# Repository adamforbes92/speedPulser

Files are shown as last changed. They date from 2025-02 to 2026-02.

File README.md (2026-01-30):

# SpeedPulser
The SpeedPulser is designed to take digital pulses from a speed sensor within the gearbox and translate this into a PWM signal which drives an OEM speedometer.  It’s perfect for situations where a physical speedometer cable cannot be installed or those wishing for a cleaner installation.  It is budget-friendly and therefore requires some final user setup and calibration.

The SpeedPulser also accepts speed signals from Can2Cluster – which can get speed from the ECU, DSG or GPS inputs.

The device takes the signals and converts them into signals to suit analog clusters – like the MK1 & MK2 Golf.  It is fully opensource and the source code can be downloaded and adjusted to suit other brands if required.  Please get in touch if you need help!

It is based on a Lolin C3 ESP32 and the BLDC motor is a TY3816B.

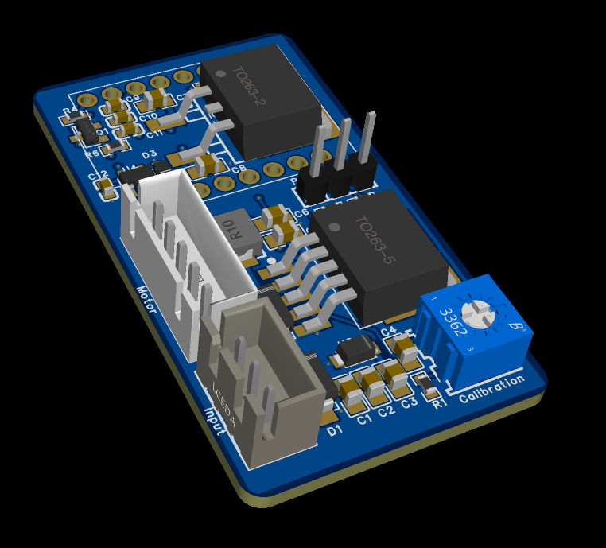
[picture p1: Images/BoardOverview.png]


### Supported Models

> MK1/MK2 Golf (120/140/160mph)
> FIAT (160mph)
> Mercedes W123/W124
> Smiths 5/8" 

Users are actively encouraged to submit new models & calibrations.

### More Detailed Instructions
The last file on GitHub is the 'Installation Guide' and provides more detail.

### Purchase
If you want to purchase an assembled SpeedPulser, you can do so here: [SpeedPulser - Forbes Automotive](https://forbes-automotive.com/products/speedpulser)

#### Installation
Only three wires are required to operate the SpeedPulser:

| Pin/ | Signal | Notes |
|-----|---|---|
| 1 | Vbatt | 12 V |
| 2 | Ground/MALT | — |
| 3 | 12v pulse | Square wave type signal |

For reference, the motor pinout is:
| Pin/ | Signal | Notes |
|-----|---|---|
| 1 | Mpwr | Black - 5-9v adjustable |
| 2 | N/A | Not used |
| 3 | Motor Direction | Green - ground to reverse |
| 4 | Motor Ground | White - motor ground |
| 5 | Motor PWM | 10kHz signal from ESP32 |

#### Pull-up or Pull-down
Different hall sensors from different manufacturers may require a pull-up or pull-down resistor.  There is a 2-way header on the board to select this.  If you find the SpeedPulser is not detecting incoming pulses, move this jumper.  Some hall sensors may have their own internal resistor, so the jumper can be removed entirely.

#### Coupler Installation
The motors will come with the coupler pre-installed and the final drive pin and securing pins separate. The end user should remove the motor and align the drive pin into the coupler and push it home. It will be a  tight fit, but a few light taps will drive it home. A spare coupler is also supplied in the kit. There should be an appreciation that the couplers are 3D printed and therefore may have some alignment variations, this is the chance to lightly heat (~100c max) to encourage/make run true. If the coupling has excessive vibration is may strip out, but a drop of superglue will repair this and run indefinitely. If this is required, ensure that the coupler runs true! Future revisions may look to replace these with a metal alternative, but this would reflect in a higher price. The point of this kit is to remain budget friendly. 

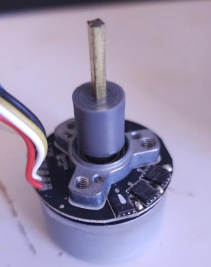
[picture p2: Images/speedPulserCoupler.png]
SpeedPulserCoupler


#### Trimming the Drive Shaft
Drive shafts are supplied in excess of required length and should be trimmed to suit each individual cluster.  Typically this is ~level with the motor housing but confirmation that it is not bottomed out is key!

#### Fine Tuning Coupler
Once the motor is built up, it can be slid over the OEM cluster. Fitment of the drive pin should be confirmed and that the motor spins freely. Some fine tuning here will keep noise to a minimum and reduce the risk of premature failure of the coupler. The drive-pin length should also be confirmed and ensure that it does engage with the cluster but does not bottom out and stop the housing seating fully. Take your time here!

#### Software Benefits
The SpeedPulser is now WiFi capable which means that all of the necessary calibration settings are available for changing in WiFi.  It will store these settings in EEPROM.  
> Fully calibrated motor: Duty Percentage vs. Resulting Speed
> Needle Sweep available
> WiFi Enabled

#### WiFi Support
WiFi is now enabled for easier on-the-fly setup.  Needle sweep & calibration can be done without needing to mess with complicated firmware.
Connect to 'SpeedPulser' on WiFi and use IP Address 192.168.1.1 in your browser to adjust settings!  WiFi is available for the first 30s after powering on the unit and will remain active when there is a connection.  This is to manage the heat generated.  Version 2 PCBs have a larger voltage step-down unit which can manage more heat.

### Initial Calibration
Initial calibration will be carried out using the WiFi feature.

> Connect to SpeedPulser on WiFi
> Go to 192.168.1.1
> Select 'Advanced Controls'
> Select the calibration you wish to use
> Choose 'Test Speed'
> Select 'Go to Speed' and choose the highest value on your cluster
> Adjust the blue potentiometer to the maximum valve
> Use 'Go to Speed' to confirm random speeds and ensure that it matches

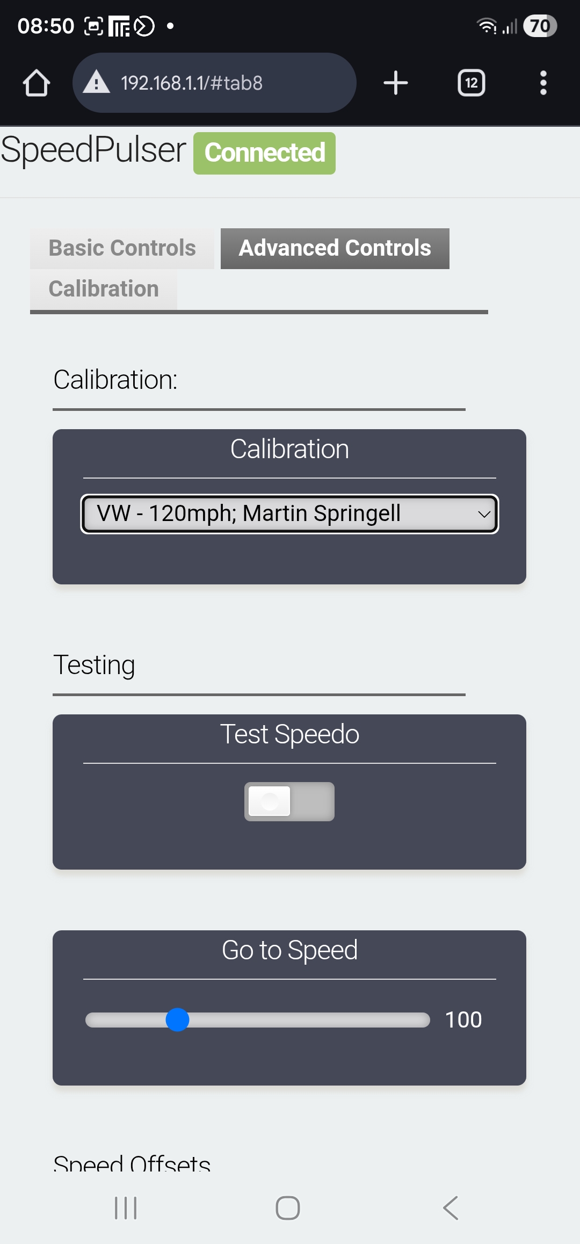
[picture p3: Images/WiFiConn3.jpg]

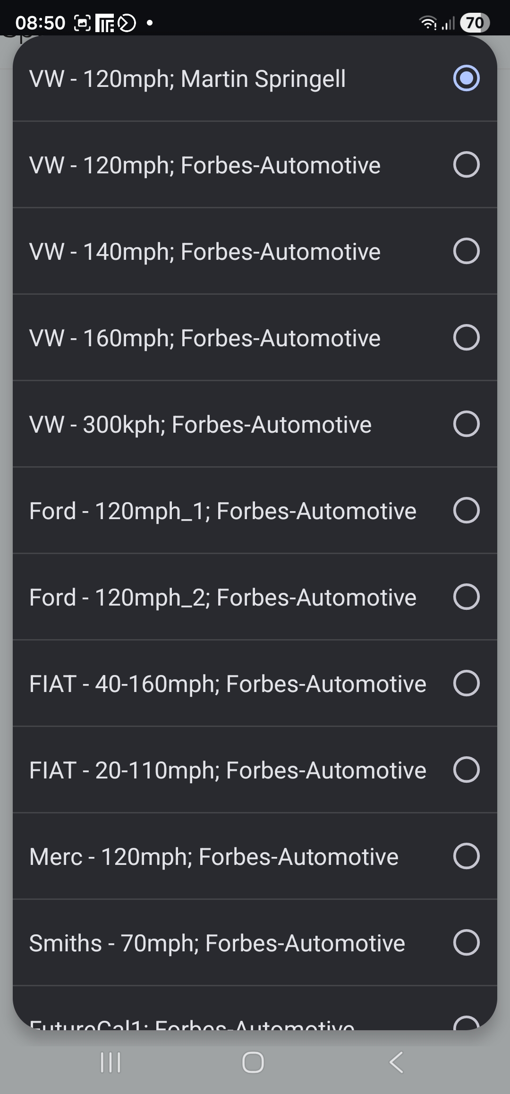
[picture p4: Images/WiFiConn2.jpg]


### Fine Tuning Calibration
If the speedometer is consistently out by a factor - the 'Offset' option can be used to adjust the speedometer.  The 'Positive Offset' switch will ADD the chosen offset.  If the switch remains off, it will SUBTRACT the chosen offset.

## Calibration of Other Speedometers

> Connect to SpeedPulser on WiFi
> Go to 192.168.1.1
> Select 'Calibration'
> Choose 'Previous' - this will roll over the duty cycle to 385 - this is the maximum speed avaiable for your calibration
> Adjust the blue potentiometer to the maximum speed you wish to calibrate to (likely the top speed of the speedometer)
> Choose 'Next' - this will reset the duty cycle back to 0 
> Choose 'Next' until the motor begins to turn.  This is the lowest speed the motor can achieve
> Begin filling the Excel sheet with each speed at each duty cycle
> Copy these values into a Word document and carry out a 'Find/Replace'.  Find "^p" and replace with ",".  This is a quick way to change all the new lines with commas
> Copy the array from Word into the suitable '_motorCal' array and upload the code
> Submit to GitHub for others to use!

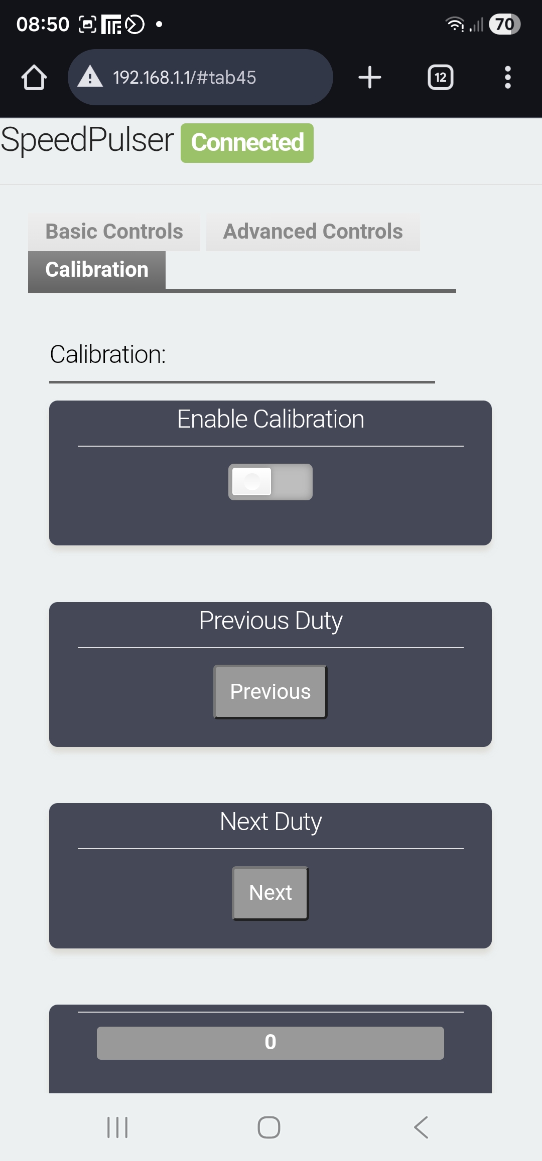
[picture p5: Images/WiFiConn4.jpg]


## Understanding the Excel
There is a plot of motor speed vs. PWM in an Excel.  Should it be required, the module can be put into 'testing mode' and each PWM variance worked through in 5 second intervals.  It takes around 10 minutes to carry out a full sweep of the available speeds, but will give good accuracy.  

## Disclaimer
It should be noted that this will drive a speedometer, but it should always be assumed that it is inaccurate and therefore no responsibilty on speed related incidents are at fault of Forbes Automotive.

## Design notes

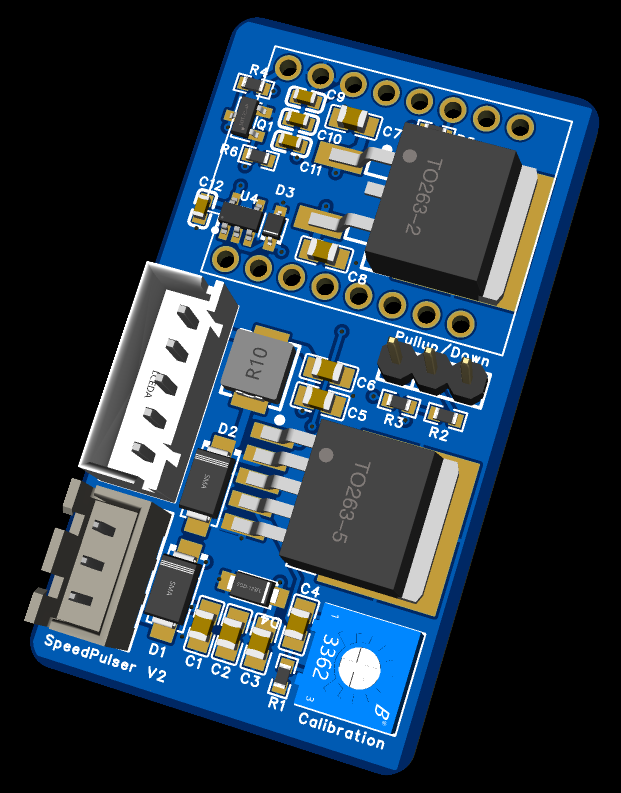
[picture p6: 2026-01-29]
Images/BoardOverview2.png

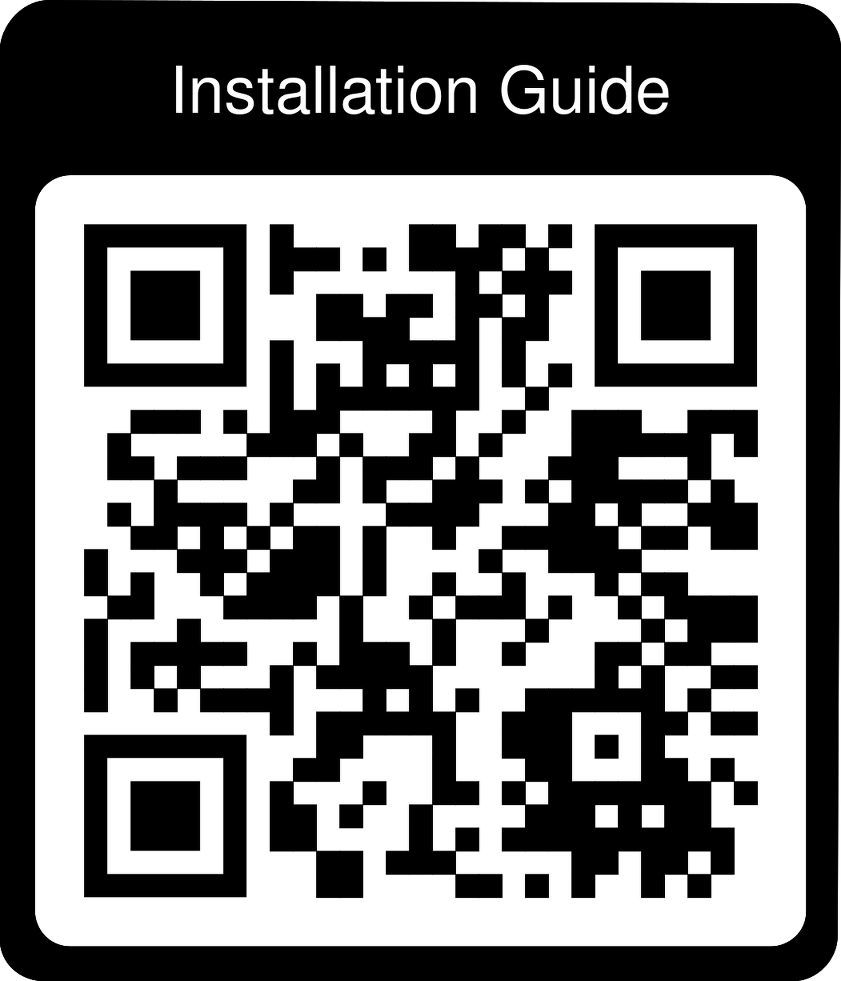
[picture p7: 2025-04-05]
Code/Untitled.jpg

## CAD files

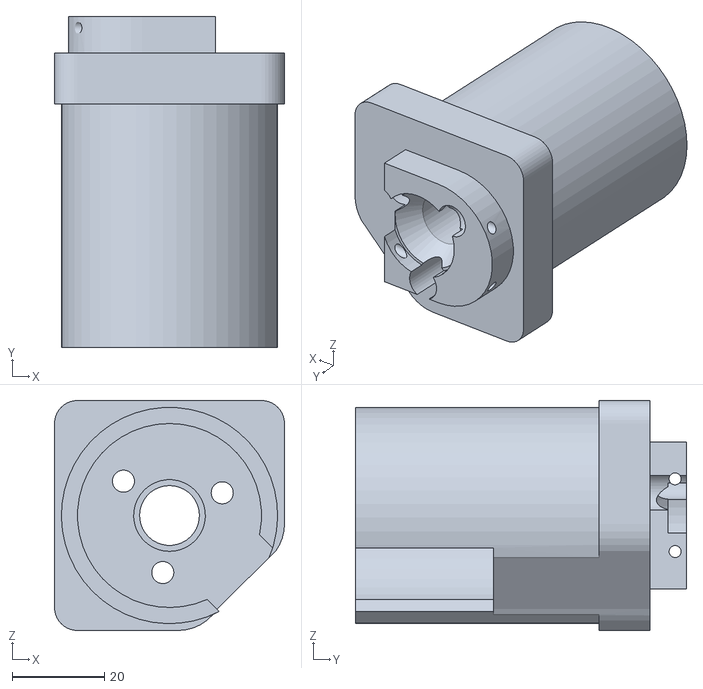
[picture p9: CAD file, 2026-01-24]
Motor Support Model/Fiat/FiatSpeedoAdapterV2.STL
50.0 x 72.0 x 50.0

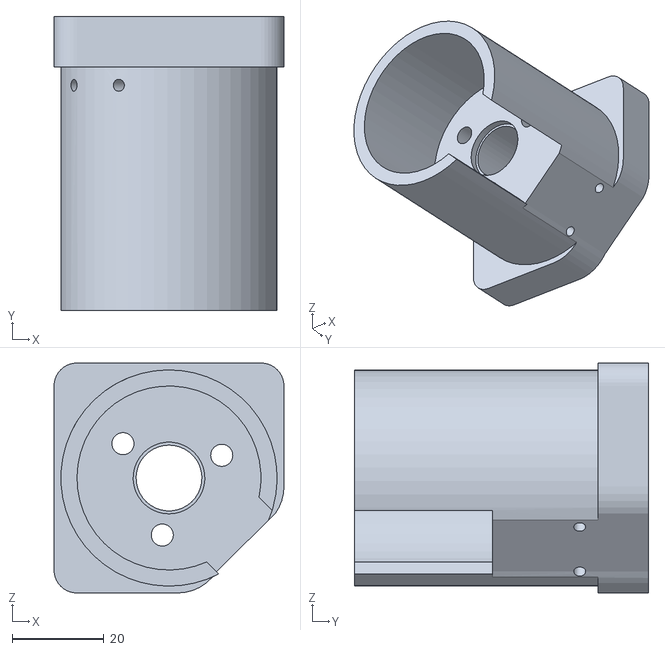
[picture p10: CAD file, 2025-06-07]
Motor Support Model/Ford/FordEscortSpeedoAdapter.STL
50.0 x 64.0 x 50.0

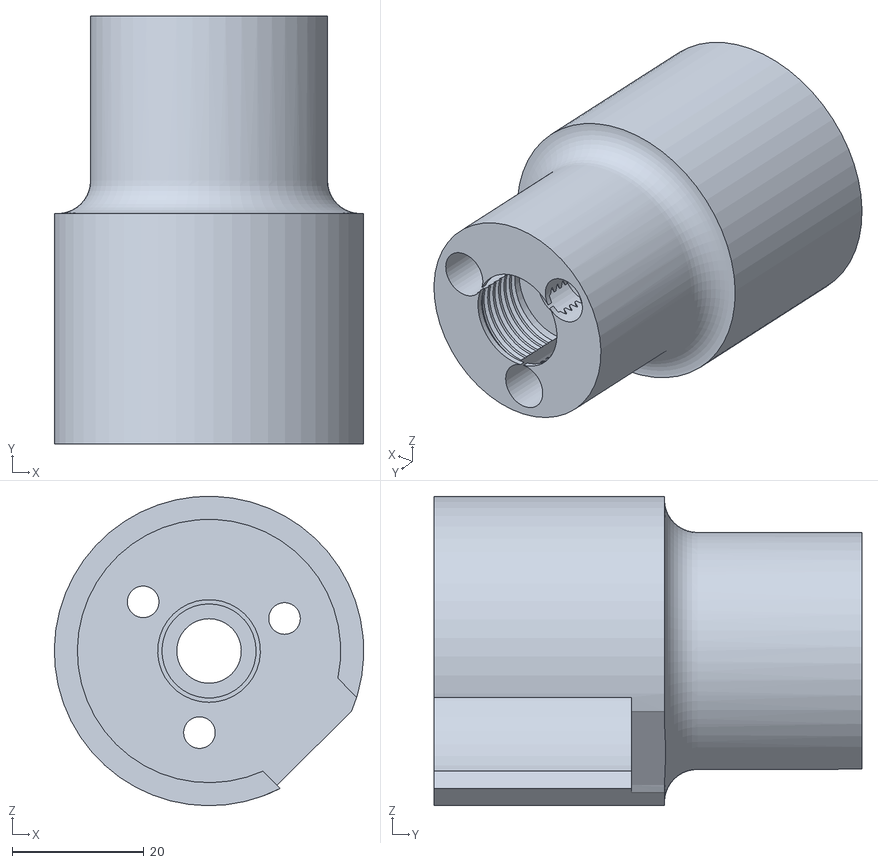
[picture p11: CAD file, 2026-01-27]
Motor Support Model/Mercedes/Mercedes W124.STL
47.0 x 65.0 x 47.0

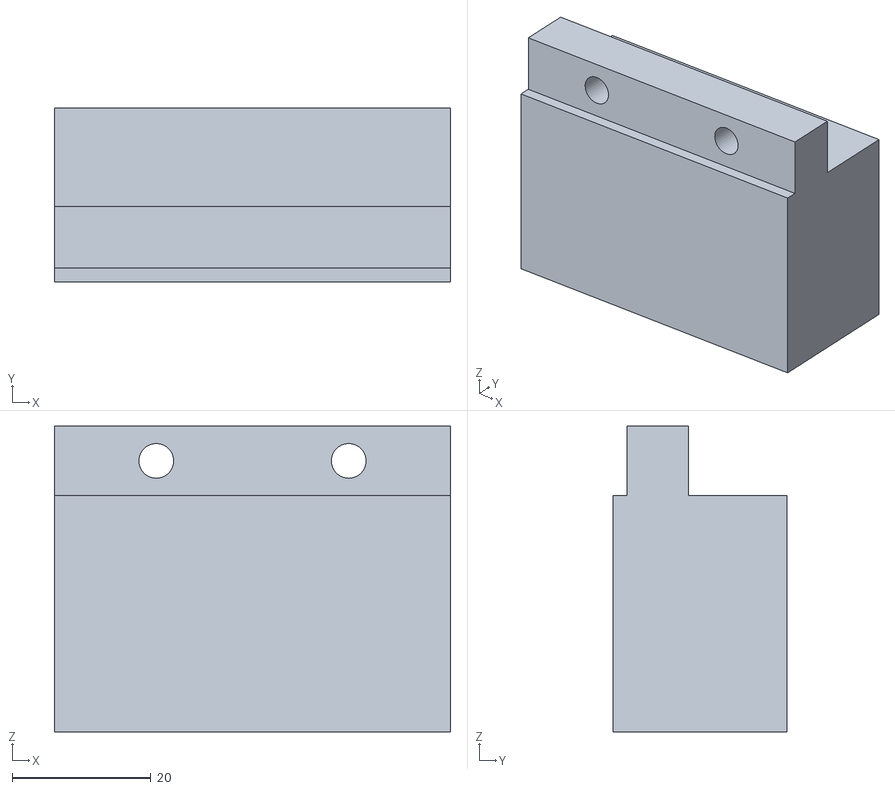
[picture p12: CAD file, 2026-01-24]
Motor Support Model/MK1GolfSpeedoAdapterBasicBoxV2.STL
57.0 x 25.0 x 44.0

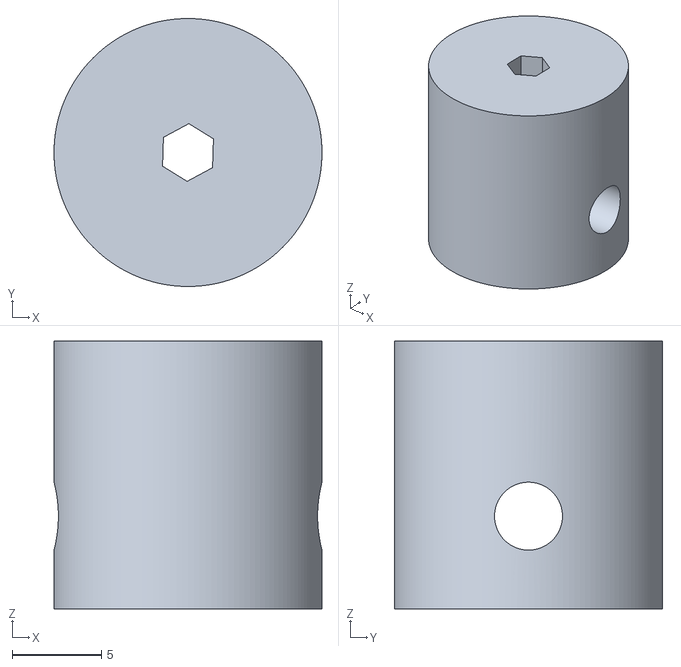
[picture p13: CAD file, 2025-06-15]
Motor Support Model/Reliant/Speedpulser drive peg.stl
15.0 x 15.0 x 15.0

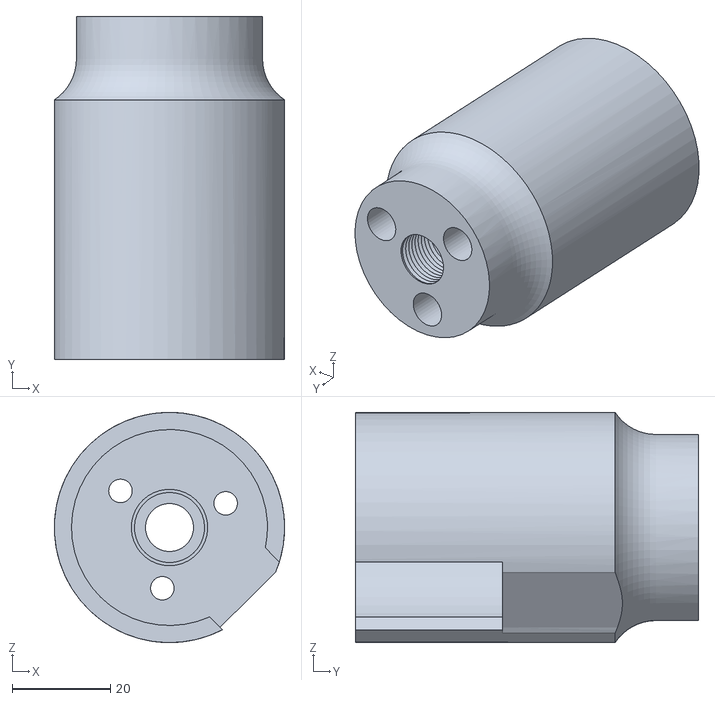
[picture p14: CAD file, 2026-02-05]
Motor Support Model/Smiths/VolvoSpeedoAdapter-M12x1.0Narrow.STL
47.0 x 70.0 x 47.0

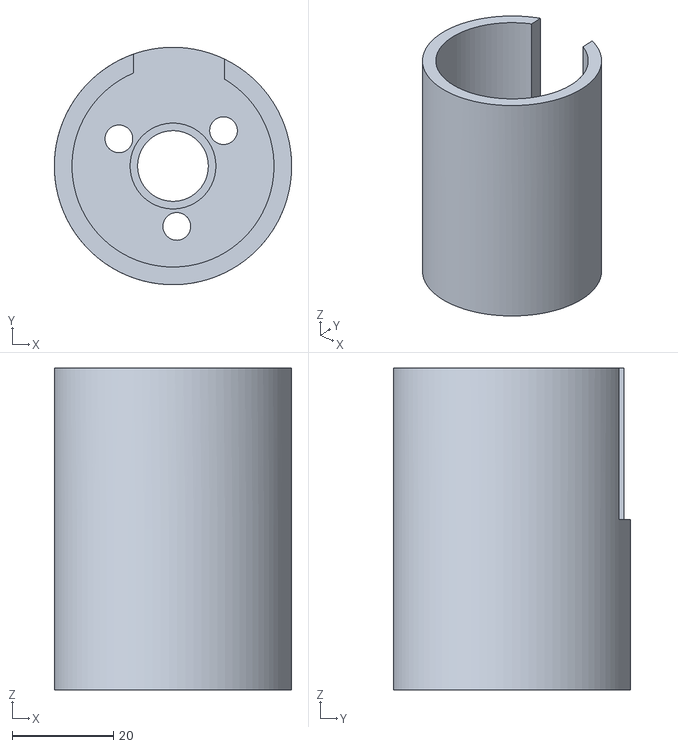
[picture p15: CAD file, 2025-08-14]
Motor Support Model/Volkswagen/MK1Threaded.stl
47.0 x 47.0 x 63.8

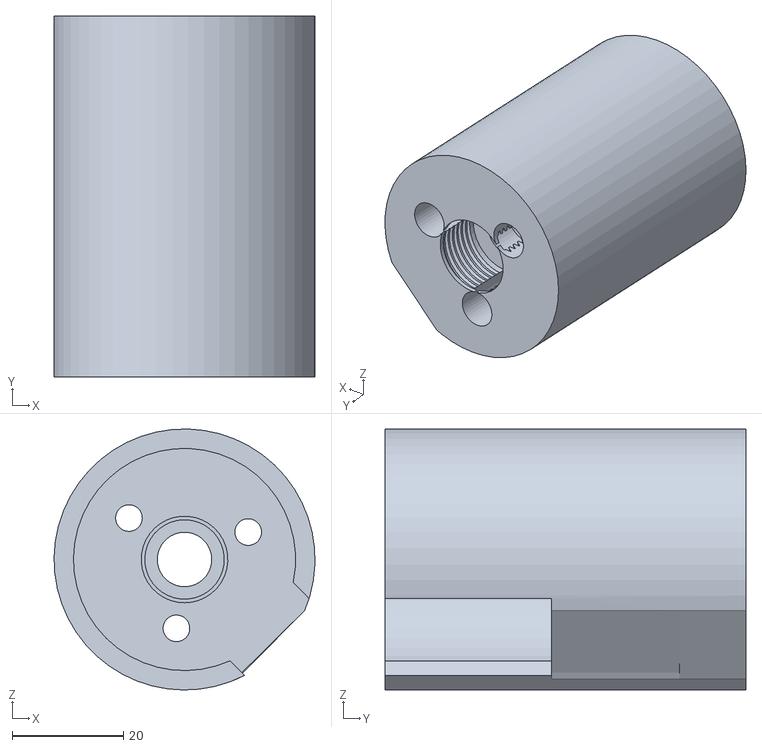
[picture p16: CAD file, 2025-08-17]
Motor Support Model/Mercedes/Mercedes W123.STL
47.0 x 65.0 x 47.0

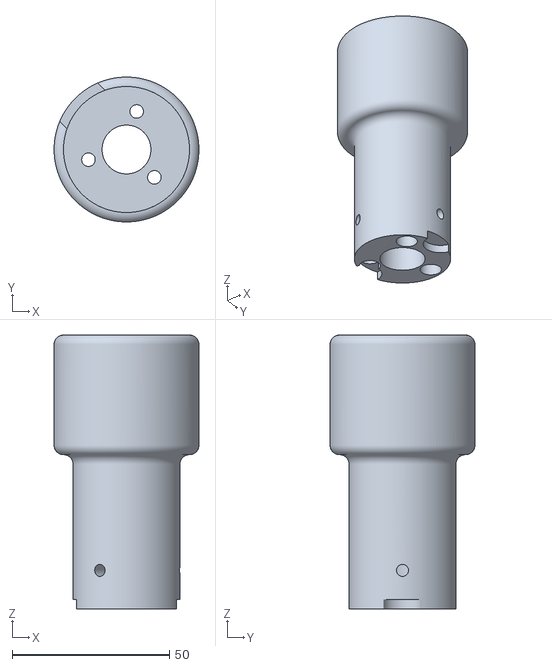
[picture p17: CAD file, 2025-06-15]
Motor Support Model/Reliant/Speedpulser to scimitar speedo.stl
46.0 x 46.0 x 87.0

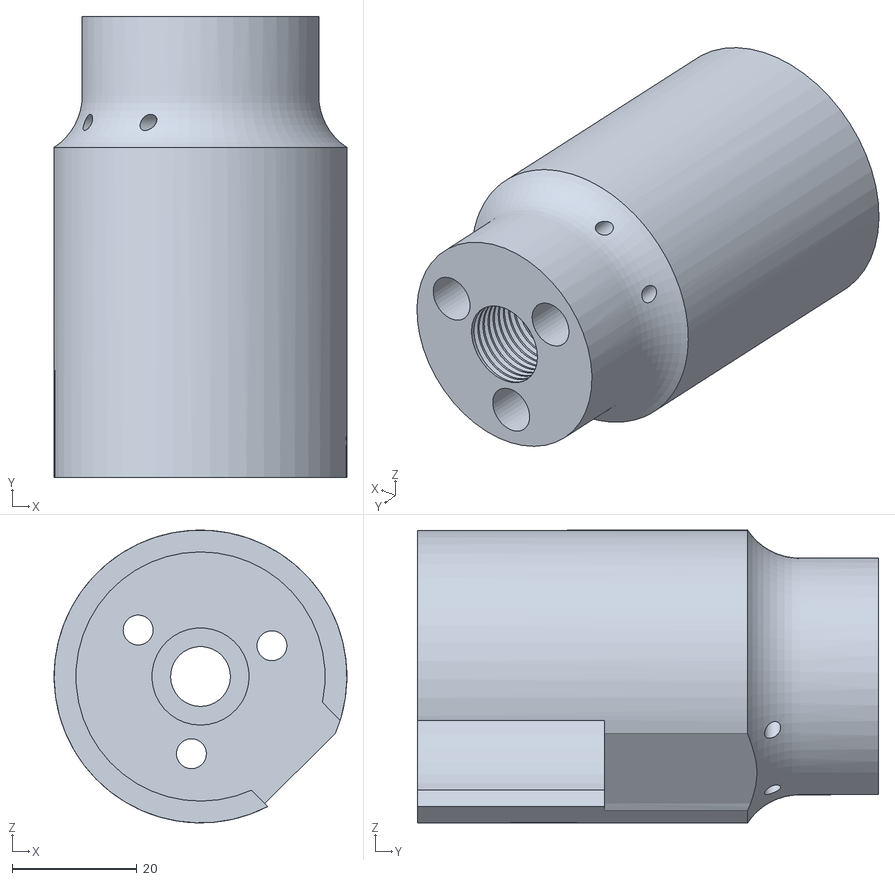
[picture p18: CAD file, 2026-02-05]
Motor Support Model/Smiths/smithsThreadedAdapter5-8sNarrow.STL
47.0 x 74.0 x 47.0

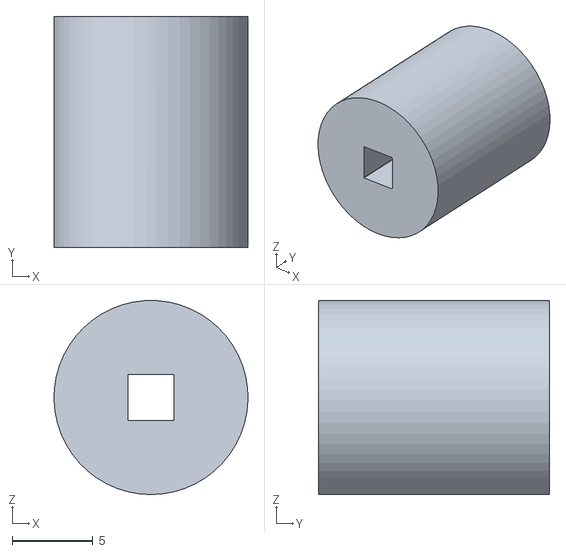
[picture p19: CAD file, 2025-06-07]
Motor Support Model/SpeedoAdapter.STL
12.0 x 14.3 x 12.0

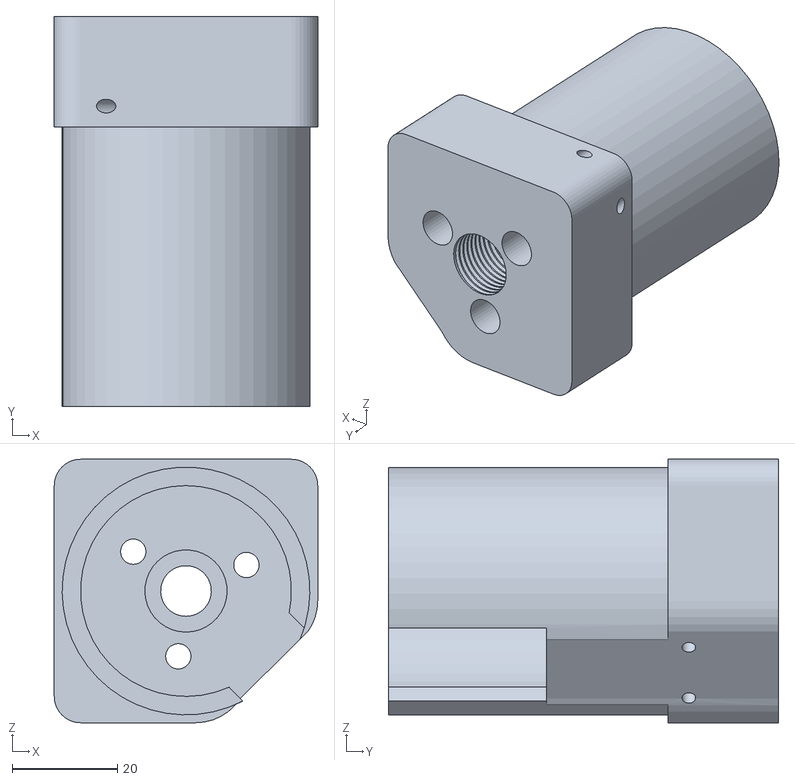
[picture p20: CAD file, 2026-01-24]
Motor Support Model/Smiths/smithsThreadedAdapter5-8s.STL
50.0 x 74.0 x 50.0

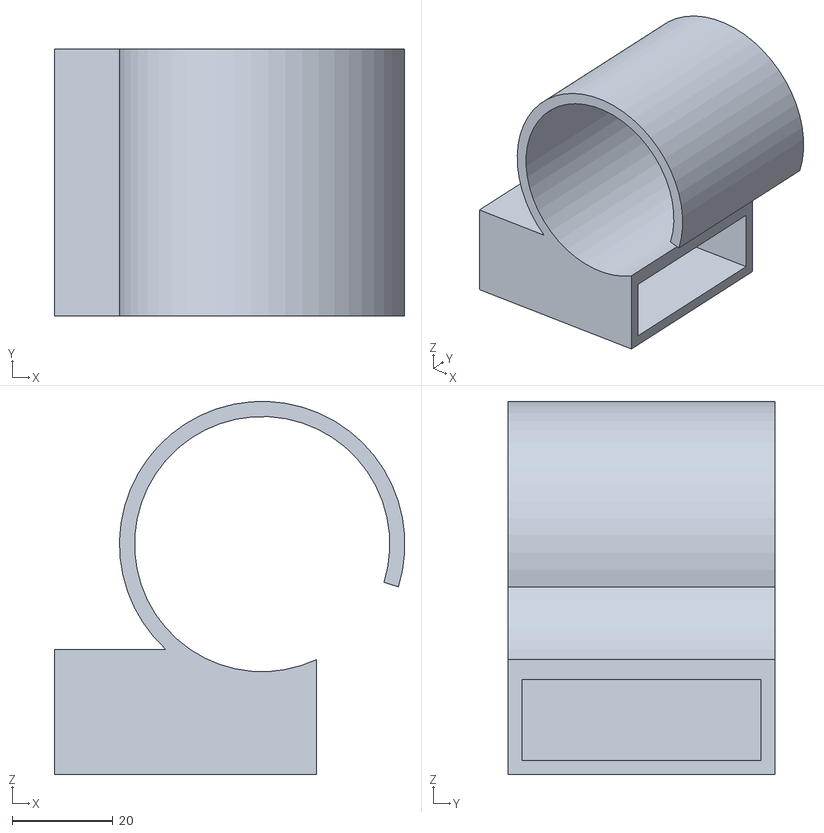
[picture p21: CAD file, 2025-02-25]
Motor Support Model/Volkswagen/MK1GolfSpeedoAdapterShield.STL
69.5 x 53.0 x 74.0

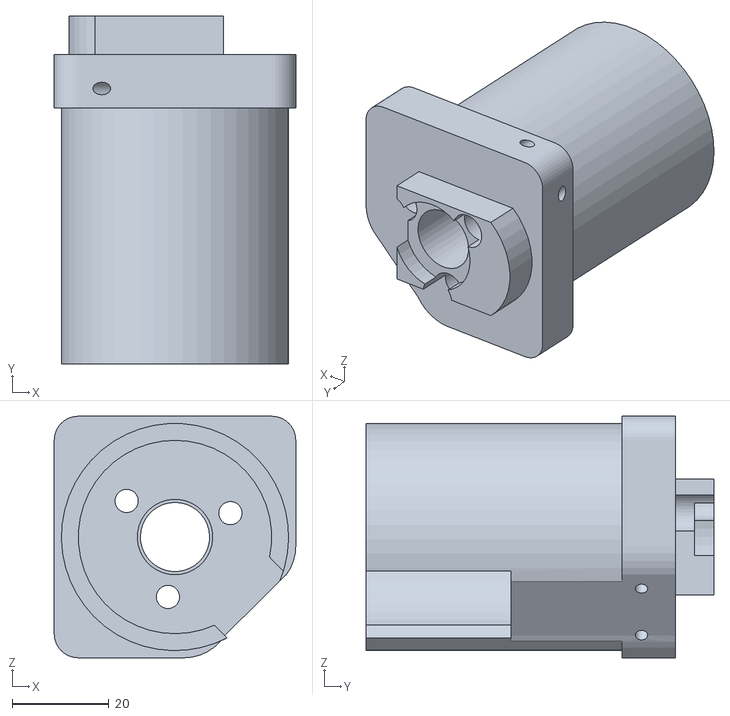
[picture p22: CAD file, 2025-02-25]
Motor Support Model/Volkswagen/MK1GolfSpeedoAdapter.STL
50.0 x 72.0 x 50.0

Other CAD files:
Motor Support Model/Ford/FordSpeedoAdapter.STL
Motor Support Model/Volkswagen/ThreadedSpeedoAdapter.STL
Motor Support Model/Fiat/FiatSpeedoAdapter.STL

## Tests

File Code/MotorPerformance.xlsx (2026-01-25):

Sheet: uint8_t
Duty Cycle (Motor) | Resulting Speed (kmh)
1 | 0
2 | 0
3 | 0
4 | 25
5 | 32
6 | 34
7 | 39
8 | 42
9 | 46
10 | 50
11 | 53
12 | 58
13 | 62
14 | 65
15 | 70
16 | 73
17 | 78
18 | 80
19 | 83
20 | 88
21 | 90
22 | 92
23 | 96
24 | 99
25 | 102
26 | 105
27 | 108
28 | 109
29 | 111
30 | 113
31 | 115
32 | 118
33 | 120
34 | 122
35 | 123
36 | 125
37 | 128
38 | 130
39 | 131
40 | 135
41 | 136
42 | 138
43 | 140
44 | 141
45 | 143
46 | 144
47 | 148
48 | 150
49 | 151
50 | 152
51 | 153
52 | 154
53 | 158
54 | 159
55 | 160
56 | 162
57 | 163
58 | 164
59 | 165
60 | 166
61 | 167
62 | 168
63 | 169
64 | 170
65 | 171
66 | 172
67 | 175
68 | 176
69 | 178
70 | 179
71 | 179
72 | 180
73 | 181
74 | 182
75 | 183
76 | 185
77 | 186
78 | 187
79 | 188
80 | 188
81 | 188
82 | 188
83 | 189
84 | 190
85 | 190
86 | 191
87 | 191
88 | 192
89 | 192
90 | 193
91 | 193
92 | 194
93 | 194
94 | 195
95 | 196
96 | 197
97 | 198
98 | 199
99 | 200
100 | 200
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

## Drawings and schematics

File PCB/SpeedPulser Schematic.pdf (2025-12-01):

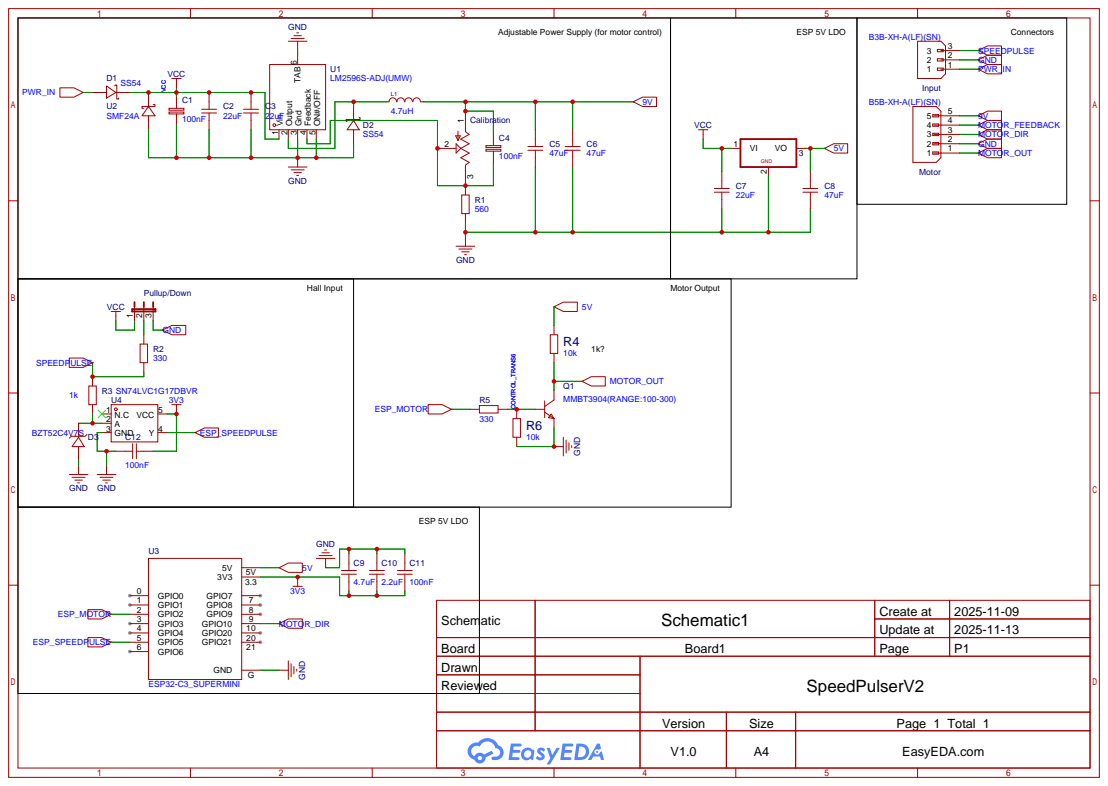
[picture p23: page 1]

Adjustable Power Supply (for motor control)

Schematic | Schematic1 | Create at | 2025-11-09

Update at | 2025-11-13

Board | Board1 | Page | P1
Drawn | | SpeedPulserV2
Reviewed

Version | Size | Page 1 Total 1
V1.0 | A4 | EasyEDA.com

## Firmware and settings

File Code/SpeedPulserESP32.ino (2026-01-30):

/*
SpeedPulser - Forbes Automotive '25
Analog speed converter suitable for mechnical drive speedometers.  Tested on VW, Ford & Fiat clusters, the only change is the CAD model. Likely compatible with other marques.  

Inputs are a 5v/12v square wave input from Can2Cluster or an OEM Hall Sensor and converts it into a PWM signal for a BLDC motor.  To get speeds low enough, the motor voltage needs reduced (hence the adjustable LM2596S on the PCB)
from 12v to ~9v.  This allows <10mph readings while still allowing high (160mph) readings.  Clusters supported are 1540 (rotations per mile) =~ (1540*160)/60 = 4100rpm

Default support is for 12v hall sensors from 02J / 02M etc: 1Hz = 1km/h.  Other marques may have different calibrations (adjustable in '_defs.h')

Motor performance plotted with Duty Cycle & Resulting Speed.  Basic Excel located in GitHub for reference - the motor isn't linear so it cannot be assumed that x*y duty = z speed(!)
LED PWM can use various 'bits' for resolution.  8 bit results in a poorer resolution, therefore the speed can be 'jumpy'.  Default is 10 bit which makes it smoother.  Both are available but 10 bit is default.

Uses 'ESP32_FastPWM' for easier PWM control compared to LEDc
Uses 'RunningMedian' for capturing multiple input pulses to compare against.  Used to ignore 'outliars'

To calibrate or adapt to other models:
> Use WiFi to enable calibration, use 'Previous' to set to 385 duty - adjust blue potentiometer to maximum speed on cluster.  Run through each duty (using 'Next'), noting down each duty vs. speed
> Copy each resulting speed into new 'motorPerformance'
> Comment out the current motorPerformance and uncomment yours
> Adjust 'maxSpeed' to suit new range 
> Done!

All main adjustable variables are in '_defs.h'.
*/

#include "SpeedPulserESP32_defs.h"

ESP32_FAST_PWM* motorPWM;                              // for PWM control.  ESP Boards need to be V2.0.17 - the latest version has known issues with LEDPWM(!)
RunningMedian samples = RunningMedian(averageFilter);  // for calculating median samples - there can be 'hickups' in the incoming signal, this helps remove them(!)
TickTwo tickEEP(writeEEP, eepRefresh);
TickTwo tickWiFi(disconnectWifi, wifiDisable);  // timer for disconnecting wifi after 30s if no connections - saves power
Preferences pref;
ESPAsyncHTTPUpdateServer updateServer;

// interrupt routine for the incoming pulse from opto
void incomingHz() {                                               // Interrupt 0 service routine
  static unsigned long previousMicros = micros();                 // remember variable, initialize first time
  unsigned long presentMicros = micros();                         // read microseconds
  unsigned long revolutionTime = presentMicros - previousMicros;  // works fine with wrap-around of micros()
  if (revolutionTime < 1000UL) return;                            // avoid divide by 0, also debounce, speed can't be over 60,000 was 1000UL
  dutyCycleIncoming = (60000000UL / revolutionTime) / 60;         // calculate
  previousMicros = presentMicros;
  lastPulse = millis();

  ledCounter++;  // count LED counter - is used to flash onboard LED to show the presence of incoming pulses
}

void setup() {
#ifdef serialDebug
  Serial.begin(baudSerial);
  DEBUG_PRINTLN("Initialising SpeedPulser...");
#endif

  readEEP();           // read the EEPROM for previous saved states
  tickEEP.start();     // begin ticker for the EEPROM
  tickWiFi.start();    // begin ticker for the WiFi (to turn off after 60s)
  updateMotorArray();  // update the motor array with the stored value from EEP

  basicInit();                                                // init PWM, Serial, Pin IO etc.  Kept in '_io.ino' for cleanliness due to the number of Serial outputs
  motorPWM->setPWM(pinMotorOutput, pwmFrequency, dutyCycle);  // set motor to off in first instance (0% duty)

  if (hasNeedleSweep) {
    needleSweep();  // enable needle sweep (in _io.ino)
  }

  connectWifi();                       // enable / start WiFi
  WiFi.setSleep(false);                //For the ESP32: turn off sleeping to increase UI responsivness (at the cost of power use)
  setupUI();                           // setup wifi user interface
  WiFi.setTxPower(WIFI_POWER_8_5dBm);  // some C3 boards require a lower Tx power otherwise it won't appear

  updateLabels();  // set base values for WiFi
}

void loop() {
  tickEEP.update();   // refresh the EEP ticker
  tickWiFi.update();  // refresh the WiFi ticker

  if (ledCounter > averageFilter) {           // only flip-flop the LED every time the filter is filled.  This will reduce the 'on' time of the LED making it easier to see!
    ledOnboard = !ledOnboard;                 // flip-flop the led trigger
    digitalWrite(pinOnboardLED, ledOnboard);  // toggle the LED to show the presence of incoming pulses
    ledCounter = 0;                           // reset the counter
  }

  // reset speed to zero if >durationReset
  if (((millis() + 10) - lastPulse) > durationReset) {
    if (!testSpeedo && !testCal) {
      motorPWM->setPWM_manual(pinMotorOutput, 0);
      ESPUI.updateLabel(label_speed, "Speed: 0");
    }
  }

  if (testNeedleSweep) { // for flag set in WiFi for testing needle sweep
    needleSweep();
    testNeedleSweep = false;
  }

  if (updateMotorPerformance) { // only refresh the motor array if cal. changed
    updateMotorArray();
  }

  // check to see if in 'test mode' (testSpeedo = 1)
  if (testSpeedo || testCal) {
    testSpeed();  // if tempSpeed > 0, set to fixed duty, else, run through available duties
  }

  if (!testSpeedo && !testCal) {
    if (dutyCycle != dutyCycleIncoming) {  // only update PWM IF speed has changed (can cause flicker otherwise)
      DEBUG_PRINTF("     DutyIncomingHall: %d", dutyCycleIncoming);
      dutyCycleIncoming = map(dutyCycleIncoming, 0, maxFreqHall, 0, maxSpeed);  // map incoming range to this codes range.  Max Hz should match Max Speed - i.e., 200Hz = 200kmh, or 500Hz = 200kmh...
      DEBUG_PRINTF("     DutyPostProc1Hall: %d", dutyCycle);

      if (rawCount < averageFilter) {
        samples.add(dutyCycleIncoming);
        rawCount++;
      }

      if (rawCount >= averageFilter) {
        dutyCycle = samples.getMedian();
        //dutyCycle = samples.getAverage();
        DEBUG_PRINTF("     getAverageHall: %d", dutyCycle);
        char buf[32];
        sprintf(buf, "Speed: %d", dutyCycle);
        ESPUI.updateLabel(label_speed, String(buf));

        if (speedOffsetPositive) {
          dutyCycle = dutyCycle + speedOffset;
          dutyCycle = dutyCycle * speedMultiplier;
          if (convertToMPH) {
            dutyCycle = dutyCycle * mphFactor;
          }
          dutyCycle = findClosestMatch(dutyCycle);
          motorPWM->setPWM_manual(pinMotorOutput, dutyCycle);
        } else {
          if (dutyCycle - speedOffset > 0) {
            dutyCycle = dutyCycle - speedOffset;
            dutyCycle = dutyCycle * speedMultiplier;
            if (convertToMPH) {
              dutyCycle = dutyCycle * mphFactor;
            }
            dutyCycle = findClosestMatch(dutyCycle);
            motorPWM->setPWM_manual(pinMotorOutput, dutyCycle);
          } else {
            motorPWM->setPWM_manual(pinMotorOutput, 0);
          }
        }

        DEBUG_PRINTF("     FindClosetMatchHall: %d", dutyCycle);
        rawCount = 0;
        samples.clear();
      }
    }
    dutyCycle = dutyCycleIncoming;  // re-introduce?  Could do some filter on big changes?  May skip over genuine changes though?
  }
}

uint16_t findClosestMatch(uint16_t val) {
  // for finding the nearest match of speed from the incoming duty.  There may be instances where the incoming speed does not equal a value in the array, so find the 'nearest' value
  // has to be 16_t due to 10 bit resolution
  // the 'find'/function returns array position, which is equal to the duty cycle
  uint16_t closest = 0;
  uint16_t closest2 = 0;
  uint16_t i = 0;
  bool speedTest = false;

  for (i = 0; i < sizeof motorPerformance / sizeof motorPerformance[0]; i++) {
    if (motorPerformance[i] > 0) {
      if (abs(val) > motorPerformance[i]) {
        speedTest = true;
        i = (sizeof motorPerformance / sizeof motorPerformance[0]);
      }
    }
  }

  if (speedTest) {
    for (i = 0; i < sizeof motorPerformance / sizeof motorPerformance[0]; i++) {
      if (abs(val - closest) >= abs(val - motorPerformance[i])) {
        closest = motorPerformance[i];
      }
    }

    for (i = 0; i < sizeof motorPerformance / sizeof motorPerformance[0]; i++) {
      if (motorPerformance[i] == closest) {
        closest2 = i;
        i = (sizeof motorPerformance / sizeof motorPerformance[0]);
      }
    }

    if (closest2 >= 385) {  // will run into the end of the array IF it's not found a speed, so return 0!
      return 0;
    } else {
      return closest2;  // else return the correct duty cycle from the found speed
    }
  } else {
    return 0;
  }
}

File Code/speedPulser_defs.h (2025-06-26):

#define _PWM_LOGLEVEL_ 0
#include "ESP32_FastPWM.h"
#include <RunningMedian.h>

// if you turn off power, unplug usb, replug usb then power it'll restart

#define baudSerial 115200  // baud rate for serial feedback
#define serialDebug 1      // for Serial feedback - disable on release(!) ** CAN CHANGE THIS **
#define testSpeedo 0       // for testing only, vary final pwmFrequency for speed - disable on release(!) ** CAN CHANGE THIS **

#define hasNeedleSweep 0  // for needle sweep ** CAN CHANGE THIS **
#define sweepSpeed 18     // for needle sweep rate of change (in ms) ** CAN CHANGE THIS **

#define incomingType 1      // 0 = Can2Cluster; 1 = hall sensor  ** CAN CHANGE THIS **
#define averageFilter 6     // number of samples to take to average/remove erraticness from freq. changes.  Higher number, more samples ** CAN CHANGE THIS **
#define durationReset 1500  // duration of 'last sample' before reset speed back to zero

#define minFreqHall 0    // min frequency for top speed using the 02J / 02M hall sensor  ** CAN CHANGE THIS **
#define maxFreqHall 200  // max frequency for top speed using the 02J / 02M hall sensor ** CAN CHANGE THIS **
#define minFreqCAN 0     // min frequency for top speed using the 02J / 02M hall sensor  ** CAN CHANGE THIS **
#define maxFreqCAN 200   // max frequency for top speed using the 02J / 02M hall sensor ** CAN CHANGE THIS **

#define minSpeed 0    // minimum cluster speed in kmh on the cluster ** CAN CHANGE THIS **
#define maxSpeed 200  // minimum cluster speed in kmh on the cluster ** CAN CHANGE THIS **

#define speedOffset 0          // for adjusting a GLOBAL FIXED speed offset - so the entire range is offset by X value.  Might be easier to use this than the input max freq.
#define speedMultiplier 1
#define speedOffsetPositive 1  // set to 1 for the above value to be ADDED, set to zero for the above value to be SUBTRACTED

#define convertToMPH 0  // for speedos that ONLY read in mph (and therefore the calibration is in mph), change KMH to find MPH
#define mphFactor 0.621371

#define pinMotorOutput 2  // pin for motor PWM output - needs stepped up to 5v for the motor (NPN transistor on the board).  Needs to support LED PWM(!)
#define pinSpeedInput 5   // interrupt supporting pin for speed input.  ESP32 C3 doesn't like them all, so if changing test this first(!)
#define pinDirection 10   // motor direction pin (currently unused) but here for future revisions
#define pinOnboardLED 8   // for feedback for input checking / flash LED on input.  ESP32 C3 is Pin 8

#ifdef serialDebug
#define DEBUG_PRINT(x) Serial.print(x)
#define DEBUG_PRINTLN(x) Serial.println(x)
#define DEBUG_PRINTF(x...) Serial.printf(x)
#else
#define DEBUG_PRINT(x)
#define DEBUG_PRINTLN(x)
#define DEBUG_PRINTF(x...)
#endif

extern unsigned long dutyCycleIncoming = 0;  // Duty Cycle % coming in from Can2Cluster or Hall
extern long tempSpeed = 0;                   // for testing only, set fixed speed in kmh.  Can set to 0 to speed up / slow down on repeat with testSpeed enabled
extern long pwmFrequency = 10000;            // PWM Hz (motor supplied is 10kHz)
extern long dutyCycle = 0;                   // starting / default Hz: 0% is motor 'off'
extern int pwmResolution = 10;               // number of bits for motor resolution.  Can use 8 or 10, although 8 makes it a bit 'jumpy'

extern int rawCount = 0;  // counter for pulses incoming
extern unsigned long lastPulse = 0;

// for 8 bit resolution
//uint8_t motorPerformance[] = { 0, 15, 20, 25, 32, 34, 39, 42, 46, 50, 53, 58, 62, 65, 70, 73, 78, 80, 83, 88, 90, 92, 96, 99, 102, 105, 108, 109, 111, 113, 115, 118, 120, 122, 123, 125, 130, 131, 135, 136, 138, 140, 141, 143, 144, 148, 150, 151, 152, 153, 154, 156, 157, 158, 159, 160, 162, 164, 166, 168, 169, 170, 171, 172, 175, 176, 178, 179, 179, 180, 181, 182, 183, 183, 184, 185, 185, 186, 186, 187, 187, 177, 189, 190, 190, 191, 191, 192, 192, 193, 193, 194, 195, 195, 196, 197, 198, 199, 200, 200 };
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

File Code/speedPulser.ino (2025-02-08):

/*
SpeedPulser - Forbes Automotive '25
VW MK1 & MK2 analog speed converter.  Takes a 5v/12v square wave input from Can2Cluster and converts it into a PWM signal for a motor.  To get speeds low enough, the motor voltage needs reduced
from 12v to 9v.  This allows <10mph readings while still allowing high (120mph) readings.

Also supports 12v hall sensors from 02J / 02M etc.

PWM for the motors supplied are based on a grounded blue wire being 100%; so this PWM lib. reads 'backwards'.
Motor slowest speed = PWM DC of 94.6% @ 1000Hz
Motor highest speed = PWM DC of 0%

Notes:
94.0% = too low(!)
93.5% = 20mph
93.0% = 20mph
90.0% = 25mph
80.0% = 43mph
70.0% = 56mph
60.0% = 73mph
50.0% = 85mph
40.0% = 

Uses 'AVR_PWM' for easier PWM control.
*/

#include "speedPulser_defs.h"

AVR_PWM* PWM_Instance;

void incomingHz() {                                               // Interrupt 0 service routine
  static unsigned long previousMicros = micros();                 // remember variable, initialize first time
  unsigned long presentMicros = micros();                         // read microseconds
  unsigned long revolutionTime = presentMicros - previousMicros;  // works fine with wrap-around of micros()
  if (revolutionTime < 1000UL) return;                            // avoid divide by 0, also debounce, speed can't be over 60,000
  dutyCycleIncoming = (60000000UL / revolutionTime) / 60;         // calculate
  previousMicros = presentMicros;
}

void setup() {
  basicInit();                                         // init PWM, Serial, Pin IO etc.  Kept in '_io.ino' for cleanliness due to the number of Serial outputs
  PWM_Instance->setPWM(pinMotOutput, frequency, 100);  // set motor to off in first instance (100% duty)
}

void loop() {
#if testSpeedo
  testSpeed();  // if tempDuty > 0, set to fixed duty, else sweep up/down
#endif

#if !testSpeedo
  if (incomingType != 0 || incomingType != 1) {
#if serialDebug
    Serial.println(F("Error! 'Incoming Type' set incorrectly!"));
#endif
  } else {
    if (dutyCycle != dutyCycleIncoming) {                                                // only update PWM IF speed has changed (can cause flicker otherwise)
      if (incomingType == 0) {                                                           // if 'Can2Cluster'
        dutyCycle = map(dutyCycleIncoming, minFreqCAN, maxFreqCAN, minSpeed, maxSpeed);  // map incoming range to this codes range.  Should match, but sense check...
        dutyCycle = map(dutyCycle, minFreqCAN, 100, motorUpperLimit, motorLowerLimit);   // re-map the range to the motor limits.  Anything after xx% = 100, anything <xx% = lowest limit (highest speed)
        
        PWM_Instance->setPWM(pinMotOutput, frequency, dutyCycle);
      }

      if (incomingType == 1) {                                                             // if 'Hall'
        dutyCycle = map(dutyCycleIncoming, minFreqHall, maxFreqHall, minSpeed, maxSpeed);  // map incoming range to this codes range.  Should match, but sense check...
        dutyCycle = map(dutyCycle, minFreqHall, 100, motorUpperLimit, motorLowerLimit);    // re-map the range to the motor limits.  Anything after xx% = 100, anything <xx% = lowest limit (highest speed)

        PWM_Instance->setPWM(pinMotOutput, frequency, dutyCycle);
      }

#if serialDebug
      Serial.println(dutyCycle);
#endif

      //dutyCycle = dutyCycleIncoming; //potentially re-introduce?
    }
#endif
  }
}

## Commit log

2025-02-25 V1.02
    Tested & working, speeds dialled in with min/max motor limits. Models listed.
    [MK1GolfSpeedoAdapter.STL, MK1GolfSpeedoAdapterShield.STL]
2025-03-01 V1.02
    Added correct IO & PWM. Revised PCB.
    [SpeedPulserESP32.ino, speedPulser_defs.h, speedPulser_io.ino]
2025-03-01 PCB
    PCB
2025-03-07 V1.02
    Added filtering, motor linearisation etc.
    [MotorPerformance.xlsx]
2025-03-27 V1.05
    Calibrated motor
2025-04-05 V1.02
    Revised code to include multiple resolutions.
    [MotorPerformance.xlsx]
2025-04-29 V1.05
    Updated for LED pulse, Fiat & Ford support.
    [FiatSpeedoAdapter.STL, FordSpeedoAdapter.STL, MotorPerformance.xlsx]
2025-05-18 V1.06
    Added global offset & reset if zero pulses.
    [SpeedPulserESP32.ino, speedPulser_defs.h, speedPulser_io.ino]
2025-06-10 V1.08
    Bug where motor would sit slightly above zero AFTER sweep. Reset motor to off after sweep.
    [SpeedPulserESP32.ino, speedPulser_defs.h, speedPulser_io.ino]
2025-06-15 V1.0
    Update to STLs
    [FiatSpeedoAdapter.STL, FordEscortSpeedoAdapter.STL, FordSpeedoAdapter.STL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]
2025-06-25 V1.09
    Added new calibration.
2025-07-15 V1.11
    Disable WiFi after 30 seconds if not used. Show current speed.
2025-08-17 Added Merc
    [Mercedes W123.STL]
2025-09-13 V1.13 - Selectable Calibration
    Added drop-down for calibration selection.
2025-09-22 V1.14
    V1.14 - added 'cannot find' speed to set to zero and low speed issues
    [SpeedPulserESP32.ino, SpeedPulserESP32_defs.h, SpeedPulserESP32_io.ino]
2025-12-01 V2
    Board update
2025-12-05 Add purchase section to README
    Added purchase information for assembled SpeedPulser.
2025-12-19 V1.16
    Added 160mph calibration and corrected incorrect scaling
    [MotorPerformance.xlsx]
2026-01-01 added 70mph Smiths cluster - uses a 5/8 18tpi housing
    added 70mph Smiths cluster - uses a 5/8 18tpi housing
    [MotorPerformance.xlsx]
2026-01-24 Added speedo adapters
    [FiatSpeedoAdapterV2.STL, MK1GolfSpeedoAdapterBasicBoxV2.STL, smithsThreadedAdapter5-8s.STL]
2026-01-25 V1.17
    Added Smiths code
    [MotorPerformance.xlsx]
2026-01-27 Added Merc W124
    [Mercedes W124.STL]
2026-02-05 Smiths 5/8s Narrow
    Smiths 5/8s Narrow
    [smithsThreadedAdapter5-8sNarrow.STL]
2026-02-05 Smiths M12x1.0, Narrow
    Smiths M12x1.0, Narrow
    [VolvoSpeedoAdapter-M12x1.0Narrow.STL]
